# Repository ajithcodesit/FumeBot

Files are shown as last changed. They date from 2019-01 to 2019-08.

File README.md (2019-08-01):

# **FumeBot**

FumeBot is a Deep Neural Network controlled robot. The mobile robot is autonomous and can be fitted with a range of sensors for different purposes. 
This was completed as the final project for Master of Science in Mechatronics at Newcastle University situated in Newcastle upon Tyne, United Kingdom. This project is a published journal at MDPI as [*FumeBot: A Deep Convolutional Neural Network Controlled Robot*](#publication).

<p align="center">
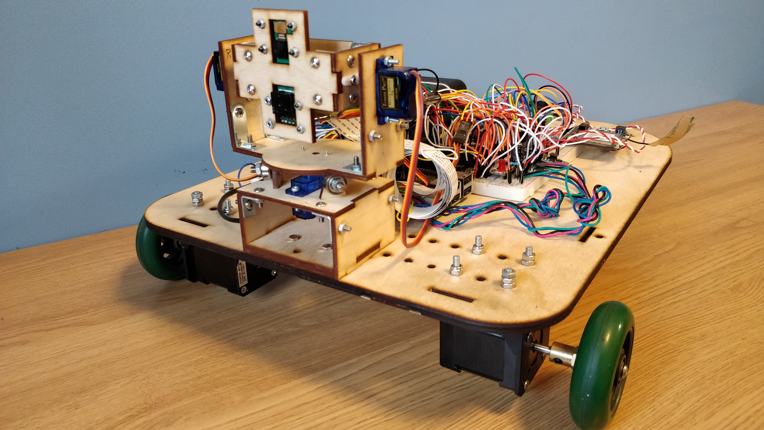
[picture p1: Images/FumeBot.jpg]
FumeBot

</p>

## Table of Contents
- [**FumeBot**](#fumebot)
  - [Table of Contents](#table-of-contents)
  - [Motivation](#motivation)
  - [Workings](#workings)
      - [The Mobile Robot](#the-mobile-robot)
      - [The Deep Neural Network](#the-deep-neural-network)
      - [The Graphical User Interface (GUI)](#the-graphical-user-interface-gui)
  - [Testing and Observations](#testing-and-observations)
  - [Requirements and Installation](#requirements-and-installation)
      - [Hardware Requirements](#hardware-requirements)
      - [Software Requirements](#software-requirements)
  - [Usage](#usage)
      - [Connecting to FumeBot](#connecting-to-fumebot)
      - [Controlling FumeBot](#controlling-fumebot)
      - [Collecting the Training Data](#collecting-the-training-data)
      - [The Deep Neural Network (AlexNet)](#the-deep-neural-network-alexnet)
      - [Data Communication and Video Transmission](#data-communication-and-video-transmission)
  - [Publication](#publication)
  - [Issues](#issues)

## Motivation

This was done as a masters final project. The idea was to check different kinds of deep neural network architectures that could be used for autonomous navigation. At the moment the only neural network that was tested is AlexNet which is a Deep Convolutional Neural Network by [Krizhvesky *et al*](https://papers.nips.cc/paper/4824-imagenet-classification-with-deep-convolutional-neural-networks.pdf).

## Workings

#### The Mobile Robot

FumeBot is a differential drive robot with a Raspberry Pi 3B and Arduino Mega 2560 on-board. The Raspberry is connected to a Raspberry Pi 5MP camera and also a Lepton 3 thermal camera. The Arduino interfaces with the stepper motor drivers, sensors and a 3G module, the data from which are sent back to the Raspberry through a UART connection. The Raspberry connects to a laptop through WiFi where the DNN is being run for inference. The DNN is being run on the laptop because if complex models are used then more processing power is available.

<p align="center">
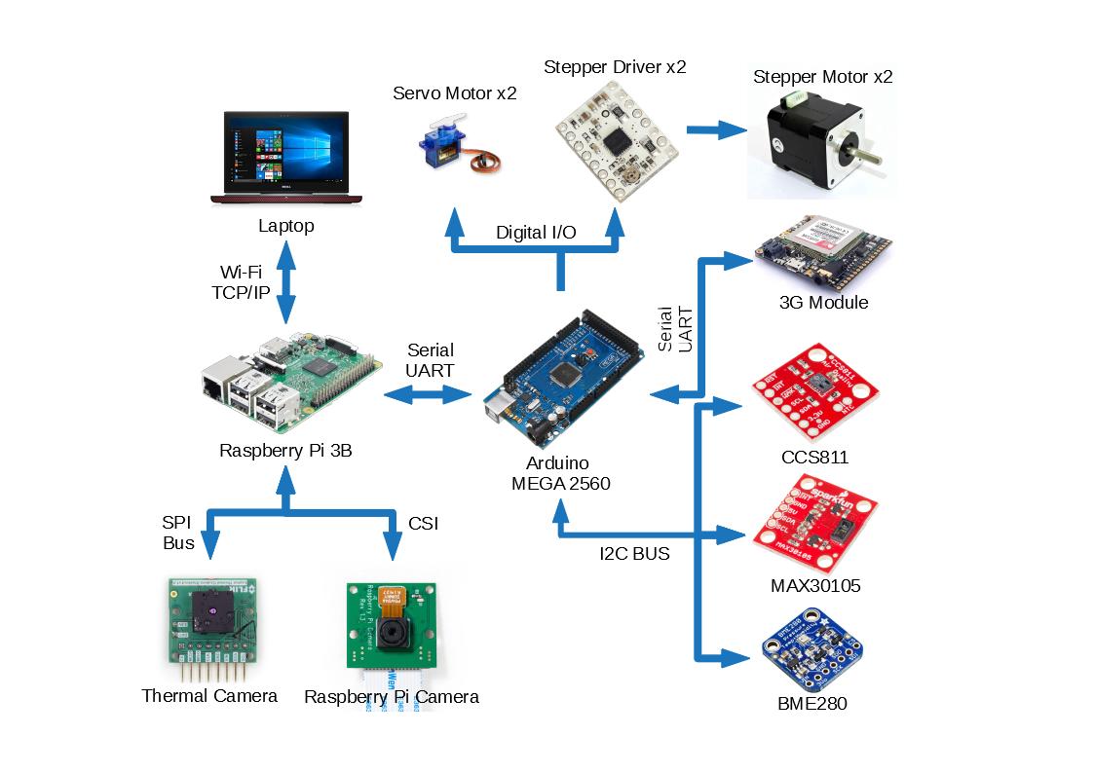
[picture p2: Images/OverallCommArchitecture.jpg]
Communication

</p>

The Raspberry Pi handles the heavy task of maintaining communication with the laptop, sending camera frames from both the RPi camera and Lepton back to the main computer. It also handles sending or receiving commands or data from the Main computer or Arduino microcontroller.

The robot is powered by two battery banks, one for driving the servo and stepper motors while the other is being used to power the Raspberry Pi 3, Arduino MCU, sensors and the 3G module. The range of motion available to the robot is shown below:

<p align="center">
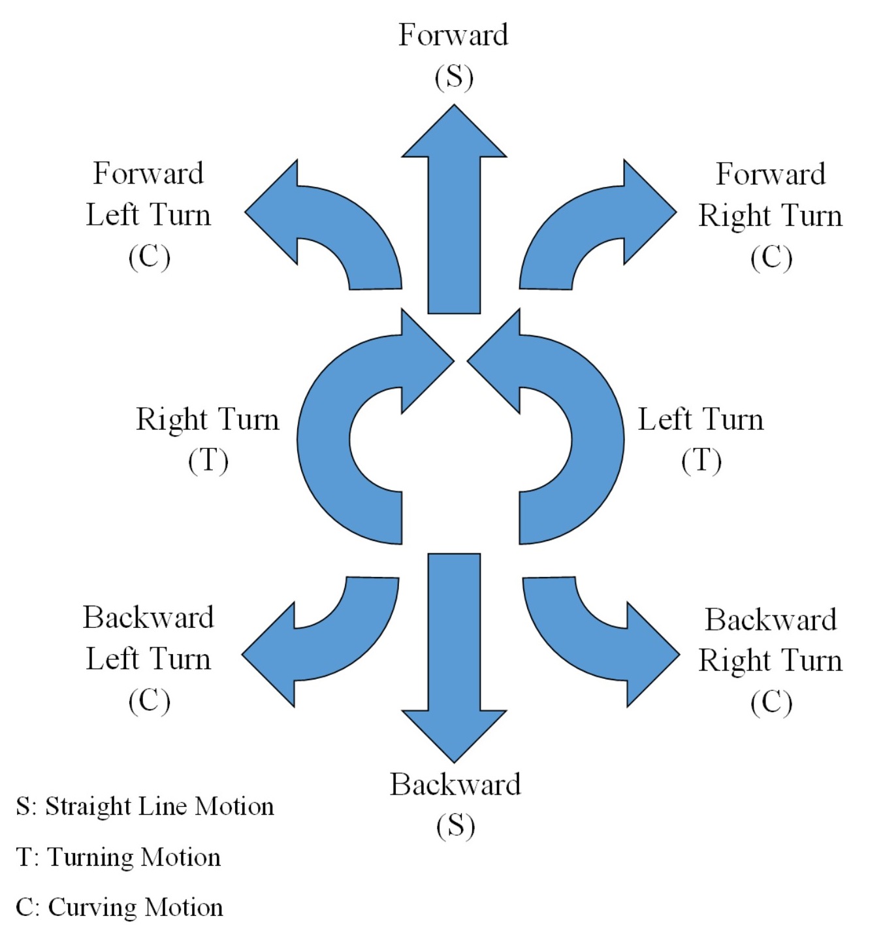
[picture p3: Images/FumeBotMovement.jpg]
Movement

</p>

In addition to controlling the robot's movement, the camera fork mount can be controlled as well to look around. The sensors carried by the robot are a gas sensor for measuring CO2 and TVOC (Total Volatile Organic Compound), particle sensor for detecting smoke and an environmental sensor for measuring pressure, temperature and humidity. Thresholds can be used to alert the user if the robot has detected smoke or high amounts of CO2 or TVOC. The alert can be sent over WiFi or through the 3G module by SMS if WiFi is not available.

#### The Deep Neural Network

As mentioned earlier the DNN used for the robot is a Convolutional Neural Network (CNN) which is a slight variation of AlexNet and can be seen in the image below.

<p align="center">
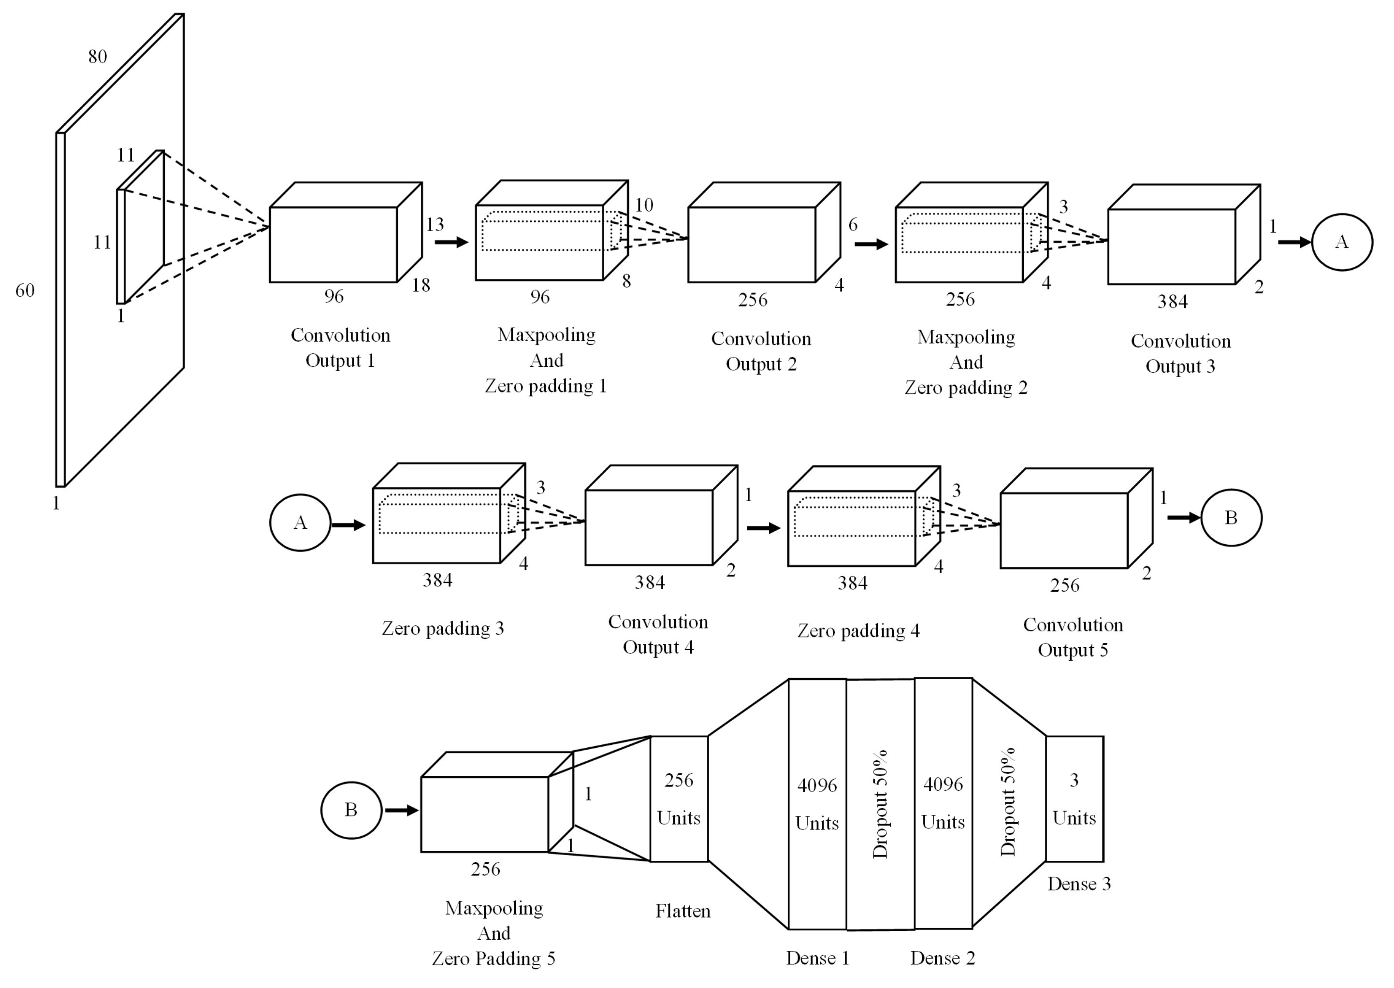
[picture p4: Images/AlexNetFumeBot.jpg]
CNN

</p>

For training the CNN, supervised learning was used in which data was collected by manually driving the robot and recording the camera frames along with the WASD key presses associated with that frame. The CNN was then trained to classify the correct key to press based on the frame received from the camera. The camera image given to the CNN was a grayscale 80x60 and the output from it is a one hot vector for example, `[0, 1, 0]` which is `[Forward left turn, Forward, Forward right turn]` of this `Forward` is selected as it is set to one.

The full range of motion available to the robot was not used to test whether the neural network could actually perform a simple task like navigating around an obstacle course. As a result only forward, forward left and forward right motion of the robot was used.

#### The Graphical User Interface (GUI)

A GUI was made to control the robot and to change the settings of the robot. The main function of the GUI is to display the image coming from the cameras, control the robot's movement and also the camera mount, record training data like the camera image and the key strokes as a one hot vector, video recording, changing the sensors thresholds and connection settings. The following is the GUI and the video stream coming from the robot displayed in the GUI respectively: 

<p align="center">
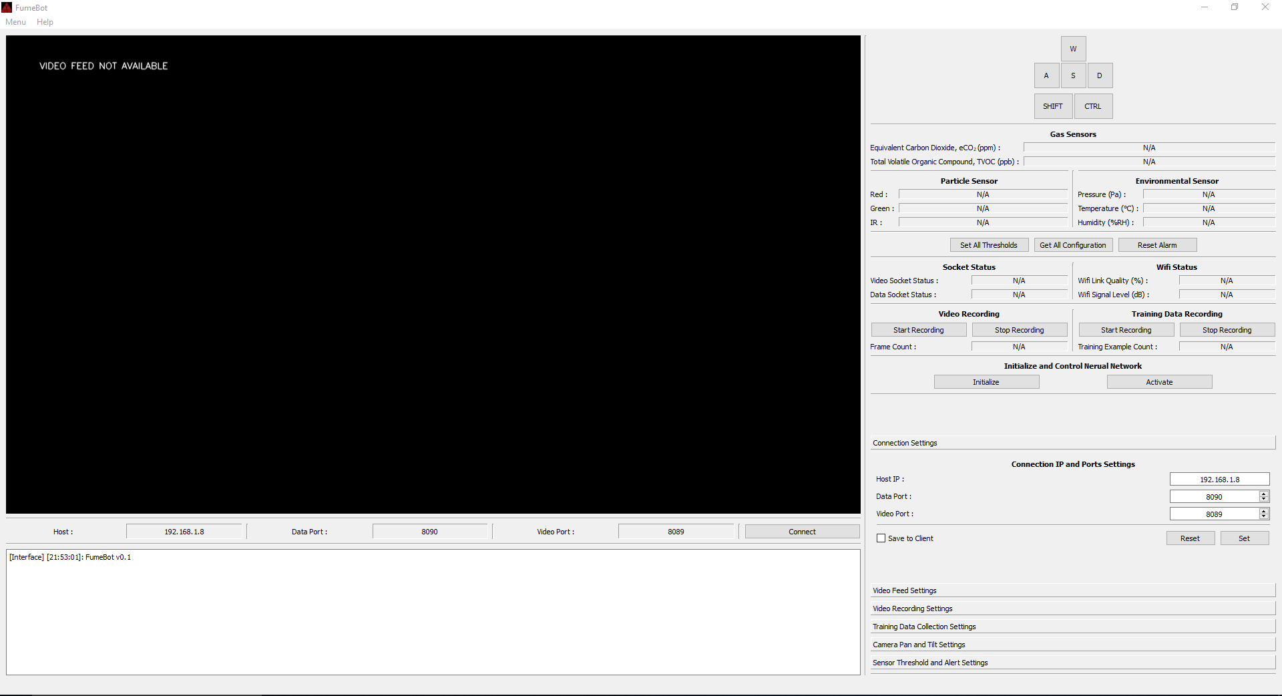
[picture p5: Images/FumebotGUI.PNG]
GUI

GUI video
<p align="center">

## Testing and Observations

The AlexNet CNN was trained on data collected from a simple obstacle course and was tested on the same and other obstacle courses to see if
it has generalized well. The obstacles when collecting the training data were orange cylinders but during testing other colors and different arrangement of
the obstacle was used to test whether it would confuse the neural network.

<p align="center">
FumeBot Lab Test Video
</p>

On testing the robot with different obstacle courses it was found that the robot has learned to navigate the courses. The obstacle color did not confuse the robot probably because grayscale images were used for training and inference which helped in not overfitting over the color of the obstacle used. But human biases
were learned by the network, for example, in order to make it obvious to the network to avoid the obstacle, it was intentionally driven up to the obstacle and avoided at the last moment which caused the neural network to follow the obstacle if moved and then avoid it. The robot was able to stay in the obstacle 
course and complete it but did make mistakes and collided with the obstacle. This is caused by not using a wide angle lens and using the standard RPi camera lens which has a limited field of view.

## Requirements and Installation

This section describes the the hardware and software requirements for FumeBot. The robot is designed in Autodesk Inventor 2018. The parts and assembly files are available [here](./FumeBot-Design/).

#### Hardware Requirements
The schematics for wiring up FumeBot can be found [here](./FumeBot-Circuit_Design/Fumebot%20Circuit.pdf).
- Raspberry Pi 3B
- Raspberry Pi Camera v1.3 (5MP)
- [FLIR Lepton 3 Camera](https://groupgets.com/manufacturers/flir/products/lepton-3-0) 
- [Adafruit FONA 3G Cellular + GPS Breakout (SIMCom SIM5320A)](https://learn.adafruit.com/adafruit-fona-3g-cellular-gps-breakout/downloads)
- Arduino MEGA 2560
- [Adafruit BME280 (Environmental Sensor)](https://www.adafruit.com/product/2652)
- [SparkFun CCS811 (Gas Sensor)](https://www.sparkfun.com/products/14193)
- [SparkFun MAX30105 (Particle Sensor)](https://www.sparkfun.com/products/14045)
- [DRV8834 Stepper Motor Driver](https://www.pololu.com/product/2134)
- [Pololu Boost Regulator](https://www.pololu.com/product/799)
- [Stepper Motors](https://www.omc-stepperonline.com/nema-17-bipolar-18deg-44ncm-623ozin-085a-53v-42x42x48mm-4-wires-17hs19-0854s.html)
- [TowerPro SG90 Servo Motors](http://www.ee.ic.ac.uk/pcheung/teaching/DE1_EE/stores/sg90_datasheet.pdf)
- BC547 Transistors
- RGB LED (Used as a status LED)

#### Software Requirements
The following software needs to be installed before running the main programs.

- For Windows PC (The GUI application was not tested on Linux)
  - OpenCV 3.4.3
  - Numpy 1.14.5
  - TensorFlow 1.10.0
  - Keras 2.2.2
  - Pandas 0.23.4 
  - PyQt4 4.11.3
  
  The above packages are for Python 3.6. Both OpenCV and PyQt4 can be installed using pip from [here](https://www.lfd.uci.edu/~gohlke/pythonlibs/). The rest can be installed by just using pip.

- For Raspberry Pi 3B (The RPi 3B application needs to be run with python 2.7)
  - PySerial 3.4
  - OpenCV 3.4.1
  - Numpy 1.14.2
  - RPI.GPIO
  
  The above packages are for Python 2.7. OpenCV needs to compiled from source and installed using instructions 
  found [here](https://www.pyimagesearch.com/2015/07/27/installing-opencv-3-0-for-both-python-2-7-and-python-3-on-your-raspberry-pi-2/). OpenCV was installed without Python Virtual Environment.

  The `FumeBot-RPi3B` file needs to be copied to `/home/pi/` directory of the Raspberry Pi and the `botsetup.sh` script should be run. This will create a service that starts every time the Raspberry boots and can be controlled using `systemctl`.

  ```bash
  # To run the script
  sudo chmod +x botsetup.sh
  ./botsetup.sh

  # To enable or disable the FumeBot service
  sudo systemctl enable fumebot.service
  sudo systemctl disable fumebot.service

  # To start or stop the FumeBot service
  sudo systemctl start fumebot.service
  sudo systemctl stop fumebot.service
  ```

- For Arduino MEGA 2560 
  - Adafruit BME280 Library
  - Adafruit FONA Library
  - SparkFun CCS811 Library
  - SparkFun MAX3010x Pulse and Proximity Sensor Library
  
  The `FumeBOT.ino` file must be flashed to the Arduino MEGA and can be found [here](./FumeBot-Firmware/FumeBOT/).

## Usage

This section describes how to use the software and to control the robot. Additional information about source code is also provided.

#### Connecting to FumeBot

The FumeBot GUI application needs to be started first by running `python FumeBot.py` on the laptop or main computer, then the connection setting needs to be changed to IP of the host computer (Laptop) to open the ports and start listening. In Window, the IP address of the machine can be found out by running `ipconfig` in command prompt and looking at the IPv4 Address section. The GUI running on the PC is the server and the Raspberry is the client, both the machines needs to have the same IP and ports for them to be able to connect. The IP and ports configuration of Fumebot can be changed in the `FumeBot-Rpi3B/bot_config.ini` file. The FumeBot service needs to be running as well.

#### Controlling FumeBot

The WASD keys can be used to control the movement of the robot and the mouse can be used to control the camera mount to tilt and pan. The mouse needs to be dragged across the video display area while holding down the left mouse button. The video capture settings can be changed to an appropriate resolution so that video lag can be reduced.

#### Collecting the Training Data

The training data recording can be started or stopped by pressing 'T' key or the "Start Recording" button can be used in the training data section. The training data is collected in the format of an image and the corresponding key pressed on receiving that image. The training data is saved as `.npy` file with an associated `.meta` file that stores the disabled keys and the order of enabled ones. For an example of reading the `.npy` file, `ViewTrainingData.py` could be run. Preprocessing maybe needed to get the data ready for training the DNN and an example of this can found in `DataSetPreprocessing.py`.

#### The Deep Neural Network (AlexNet)

The AlexNet CNN model is defined in `DeepNeuralNetworkModel.py` the methods of which are loaded into `FumeBotGUI/FumeBotDNN.py`. The model is loaded and weights are applied in the constructor of the `FumeBotDNN` class. The `dnn_prediction_function` is used for inference and the output of this function is the required key the CNN wants to send to the robot. The key classification should be a one-hot vector, for example, `[1, 0, 1]`. The predicted key press vector is emitted as a signal in PyQt to the main GUI application and is handled by the `handle_dnn_key_press` function.

For inference on images coming from the robot, the DNN must be first initialized by pressing the 'I' key or "Initialize" button. To start the prediction the 'N' key can be used to toggle it or "Activate" button can be pressed. The `FumeBotDNN.py` is loaded into the main GUI application `FumeBot.py` in which the `dnn_prediction_function` mentioned earlier is run inside the `update_video_feed_display` function.

#### Data Communication and Video Transmission

The data communication and reception of video stream is done in `FumeBotGUI/FumeBotSockComm.py`. The handling of data is done in the `handle_socket_data` function and the image frames from the camera is handled in the `get_socket_stream_frames` function in the main GUI. The data is exchanged between the `FumeBotSockComm.py` and `FumeBot.py` in the form of PyQt signals as mentioned above in the case of the DNN.

The frames coming from the camera are in JPEG format and is then rendered in the GUI video frame. The figure shown below shows how the video is sent from the client (Robot) to the Server (Fumebot GUI application). Both the RPi camera and the Lepton thermal camera follows the same procedure for transmission of video.

<p align="center">
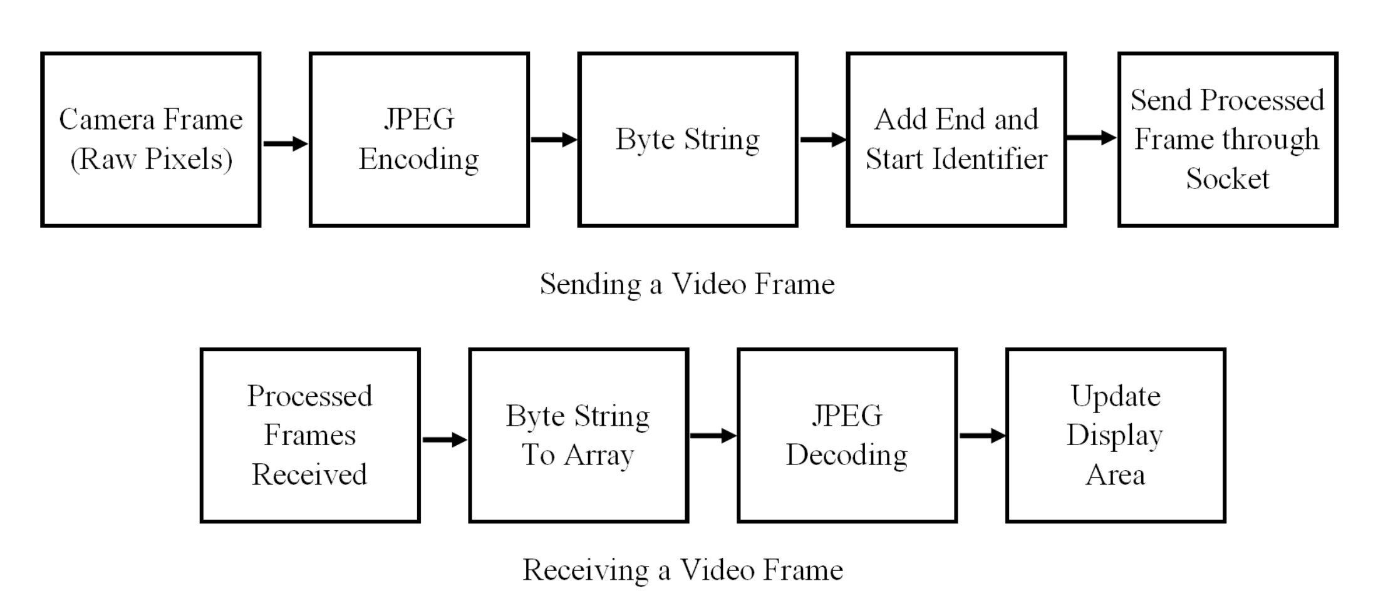
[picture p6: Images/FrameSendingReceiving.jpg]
Video TX RX

</p>

If other data needs to be sent from the robot, the `handle_socket_data` function needs to be modified. All the data communication from the Raspberry and Window PC needs to be in the following format:
```
$<CMD>,<DATA1>,<DATA2>,…,<DATA(n-1)>,#
```
Data communication between the Raspberry and Arduino is in the following format:

```
<CMD>,<DATA1>,<DATA2>,…,<DATA(n-1)>,\n
```
All the data are sent and received in plain string format.

## Publication

[Thomas, A.; Hedley, J. FumeBot: A Deep Convolutional Neural Network Controlled Robot. *Robotics* **2019**, 8, 62.](https://doi.org/10.3390/robotics8030062)

## Issues

The following are some of the know issues observed during testing.

- The `FumeBotMain.py` which is ran on the client side can sometimes crash with an error caused by OpenCV.
- Python 2.7 is used in the client side because OpenCV could not be installed for Python 3.6. Later this was resolved but not tested. 
- The FLIR Lepton 3 thermal camera module freezes after a few minutes of usage. 
- Data built up in the client side causes a lag in getting the real time sensor measurements displayed on the GUI.
- The initialization of the DNN is slow.
- Saving the training data takes a long time if the data held in the list is large.

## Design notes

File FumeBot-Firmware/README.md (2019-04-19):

## **Additional Information about the Firmware**

#### Firmware Usage
The `FumeBOT` folder needs to be opened in Arduino 1.8.7 or higher and the `FumeBOT.ino` file needs to be flashed to
an Arduino MEGA 2560 only. This is because the timers of the microcontroller are now used for generating the square wave required to drive the stepper motor and registers specific to the Atmel ATmega2560 microcontroller are changed.

#### Modification to Servo Libraries
The above modification to the timer register meant some changes needed to be applied to the `Servo.cpp`, `Servo.h` and `ServoTimers.h` files. The changes to these files are necessary because all the timers in the microcontroller are initially setup to generate PWM outputs and the above register modification to generate a required frequency square wave interferers with servo library timer setup. The library is also required to control the pan and tilt servos for the camera fork mount.

To fix the above-mentioned problems, a copy of the servo library was made and altered to not make use of the timers required to generate the square wave for the stepper drivers. The libraries were then renamed to `ServoMod.cpp`, `ServoMod.h` and `ServoTimersMod.h` so that it does not interfere with the original servo libraries provided by Arduino. This was done instead of modifying the original servo libraries because the changes were only needed for this application.

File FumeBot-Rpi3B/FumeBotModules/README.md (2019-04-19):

## **Modules for Mobile Robot Side**

#### Communication modules for the Robot
The communication between the robot and GUI application is achieved by using the `FumeBotSocketComm.py` which uses TCP sockets for streaming data. On the other hand the communication between the Raspberry Pi and the Arduino microcontroller is realized through `FumeBotSerialComm.py` module. The serial communication is through a standard UART port available on both the Arduino MEGA and Raspberry Pi. 

The default UART available on Raspberry Pi 3B GPIO is the Mini UART which is inferior compared to the UART used for the Bluetooth modem. Therefore, the UARTs are switched so that the better one is available at the GPIO. More information on how to do this is available by following this [link](https://www.raspberrypi.org/documentation/configuration/uart.md).

#### The FLIR Lepton 3 Module
To communicate with the Lepton 3 thermal camera the `Lepton3capture.c` was slightly modified from the original available [here](https://github.com/lukevanhorn/Lepton3/blob/master/capture/capture.c). Since the main program for the robot is written in python the `Lepton3capture.c` file is compiled into shared object file and is then loaded into `Lepton3CapLib.py` python module which breaks out the necessary functions available in the original C file. The `Lepton3CapLib.py` file is then imported by `FumeBotSocketComm.py` to get the frames from the thermal camera in a thread and send it to the GUI application.

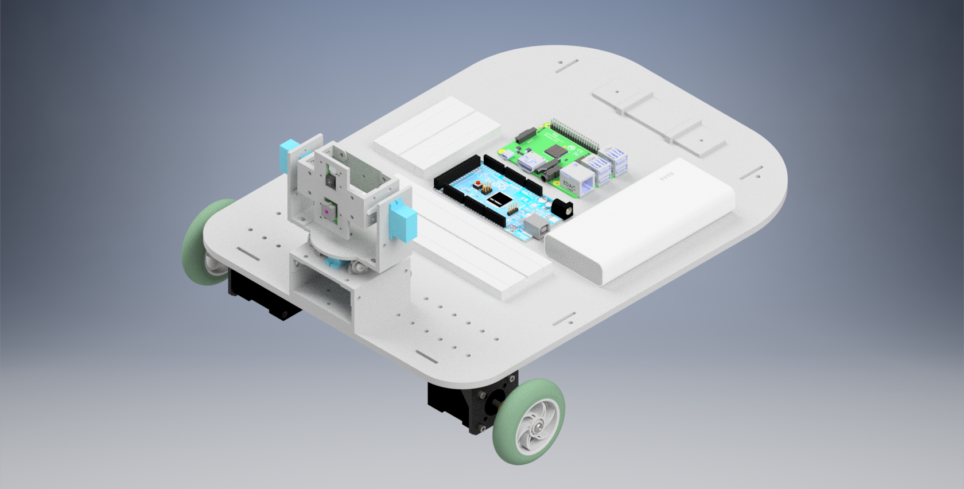
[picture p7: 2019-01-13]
FumeBot-Design/Renders/FumeBOT Fork Mount - isometric view.png

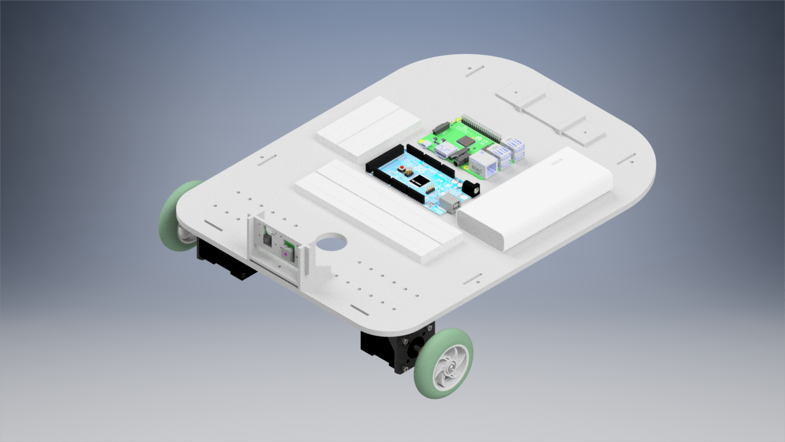
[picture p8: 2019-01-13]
FumeBot-Design/Renders/FumeBOT- isometric view.png

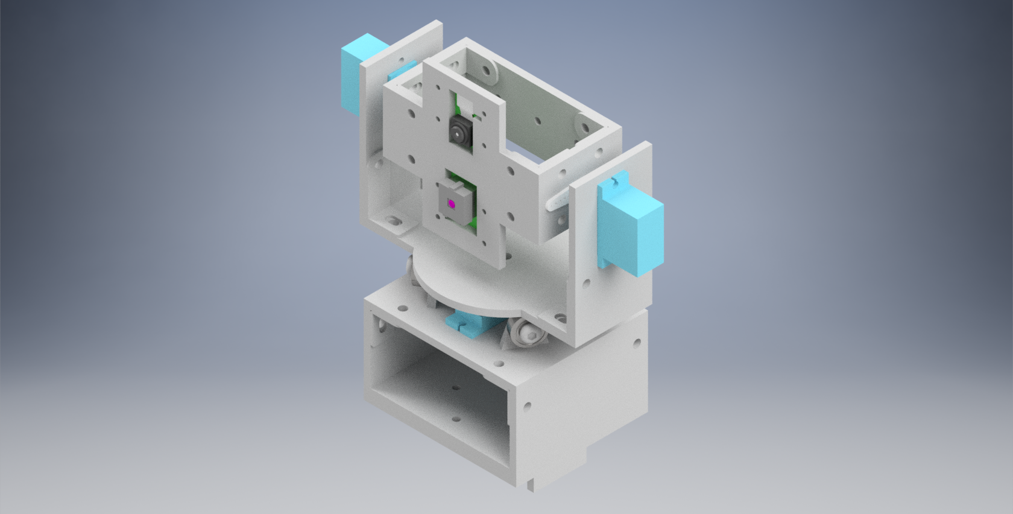
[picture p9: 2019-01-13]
FumeBot-Design/Renders/Fork Mount - isometric view.png

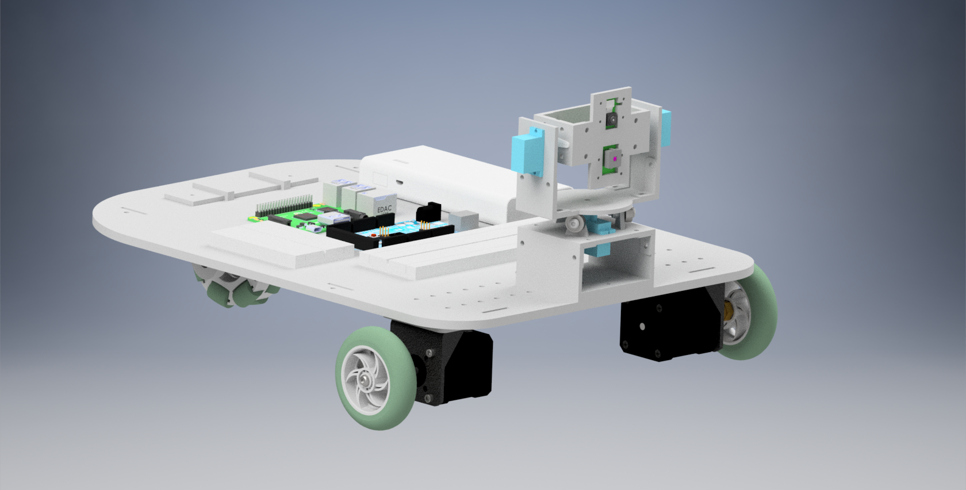
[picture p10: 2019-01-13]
FumeBot-Design/Renders/FumeBOT Fork Mount - low angle view.png

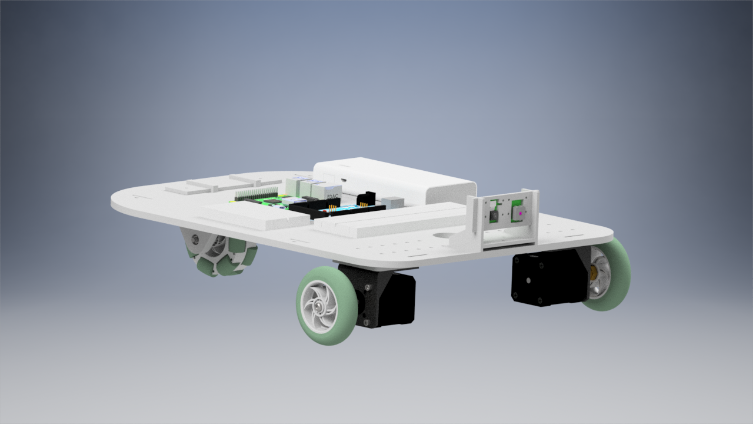
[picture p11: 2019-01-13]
FumeBot-Design/Renders/FumeBOT - Low angle view.png

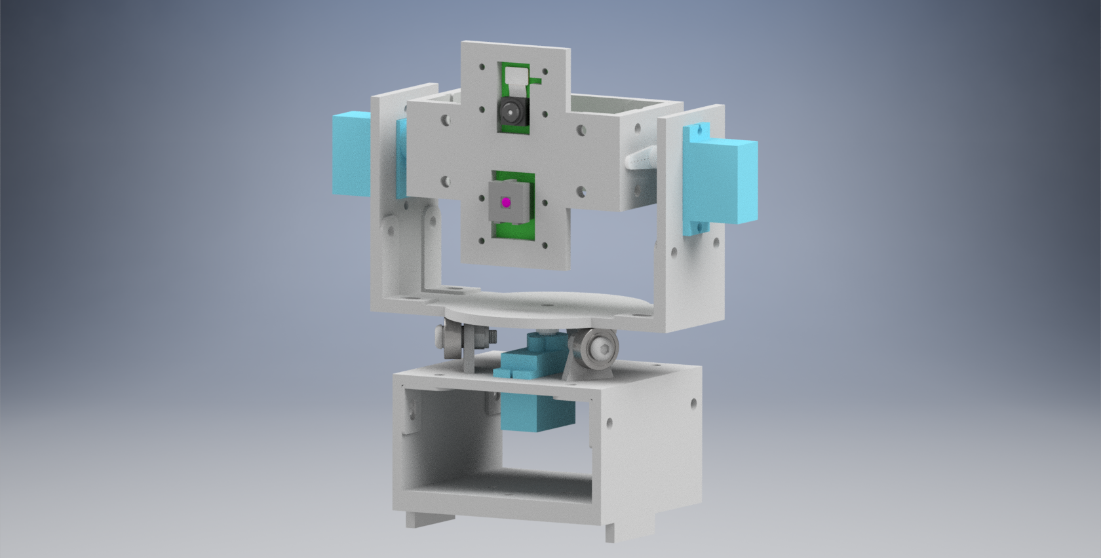
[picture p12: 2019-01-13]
FumeBot-Design/Renders/Fork Mount - Low angle view.png

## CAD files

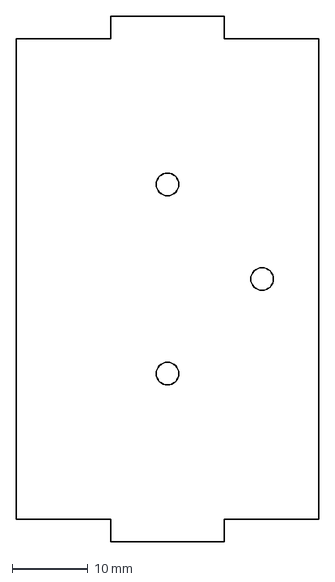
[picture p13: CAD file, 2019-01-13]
FumeBot-Design/DXF files/Mobile Bot Chassis DXF files/Camera cross bar-3mm-x1.dxf
40.0 x 69.5 mm

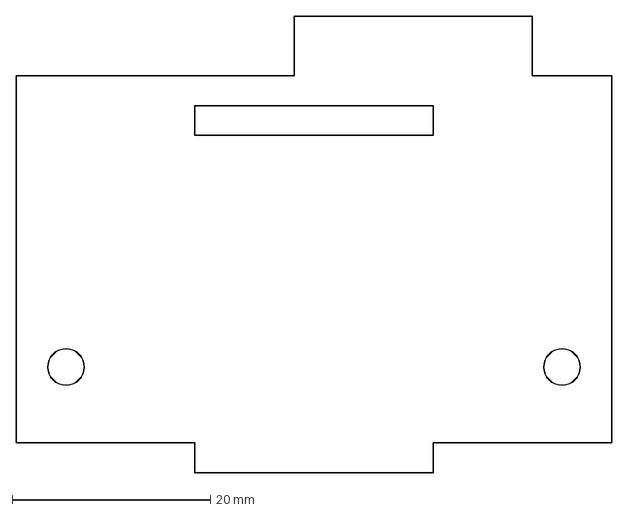
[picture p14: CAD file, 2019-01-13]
FumeBot-Design/DXF files/Pan and Tilt DXF files/Pan base top side bars-3mm-x2.dxf
60.0 x 46.0 mm

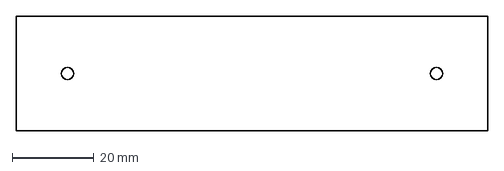
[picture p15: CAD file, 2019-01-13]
FumeBot-Design/DXF files/Mobile Bot Chassis DXF files/Mecanum support lock bar-3mm-x1.dxf
115.0 x 28.0 mm

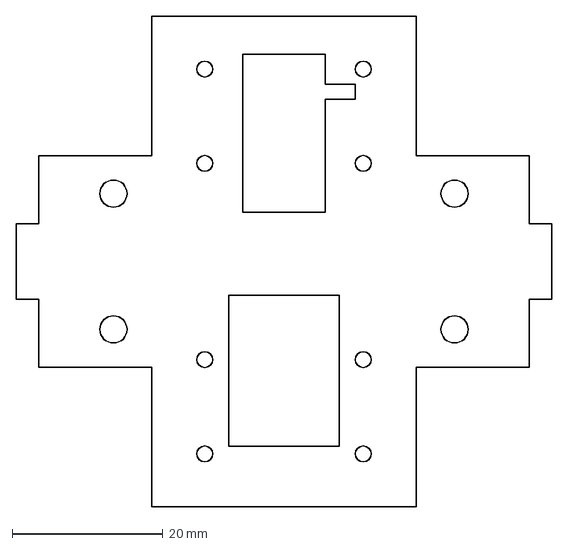
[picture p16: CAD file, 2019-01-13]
FumeBot-Design/DXF files/Pan and Tilt DXF files/Camera holder plate-3mm-x1.dxf
71.0 x 65.0 mm

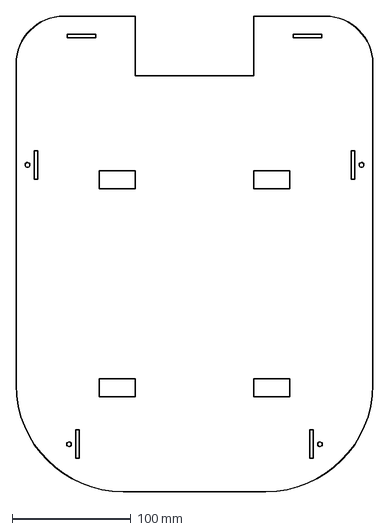
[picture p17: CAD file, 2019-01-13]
FumeBot-Design/DXF files/Mobile Bot Chassis DXF files/Top plate-3mm-x1.dxf
300.0 x 400.0 mm

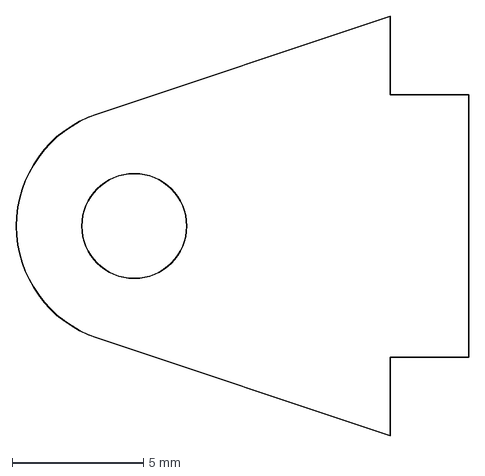
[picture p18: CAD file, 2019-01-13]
FumeBot-Design/DXF files/Pan and Tilt DXF files/Bearing risers-3mm-x3.dxf
17.2 x 16.0 mm

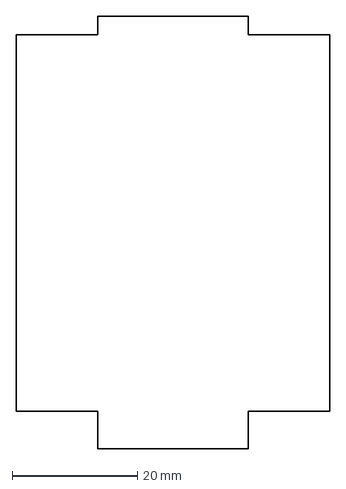
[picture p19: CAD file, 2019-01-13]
FumeBot-Design/DXF files/Mobile Bot Chassis DXF files/Base and top seperator-3mm-x6.dxf
50.0 x 69.0 mm

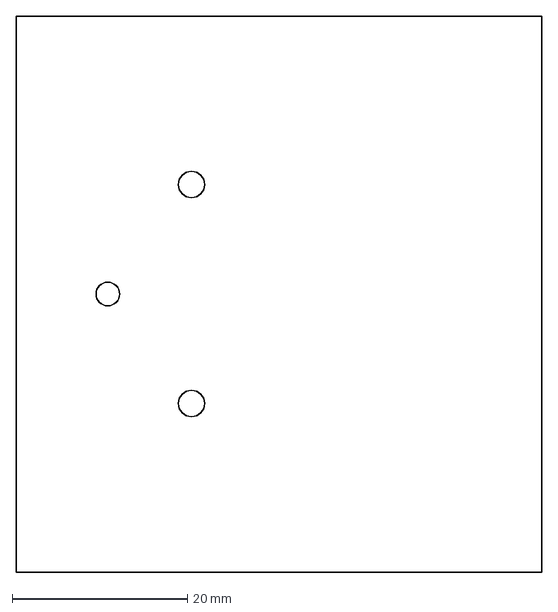
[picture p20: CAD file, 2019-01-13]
FumeBot-Design/DXF files/Pan and Tilt DXF files/Pan cross bar spacer-3mm-x1.dxf
60.0 x 63.5 mm

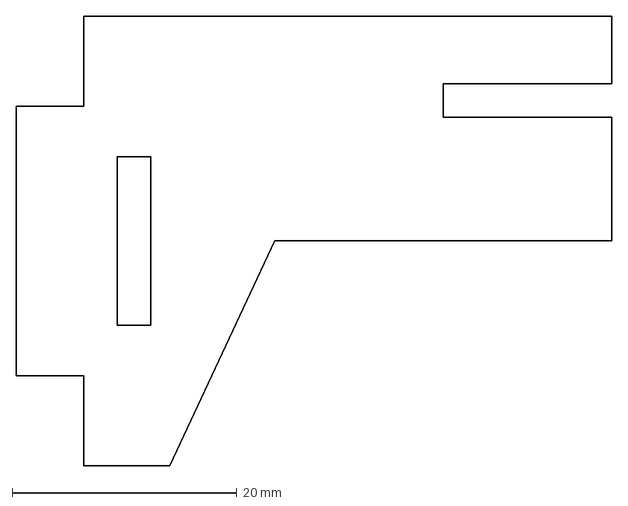
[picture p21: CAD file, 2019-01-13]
FumeBot-Design/DXF files/Mobile Bot Chassis DXF files/Camera bracket raiser-3mm-x2.dxf
53.0 x 40.0 mm

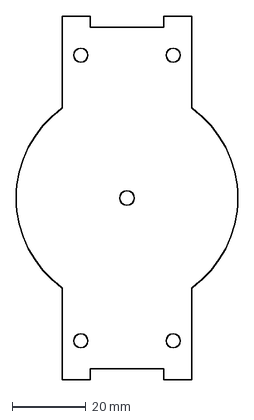
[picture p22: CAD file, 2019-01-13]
FumeBot-Design/DXF files/Pan and Tilt DXF files/Camera raiser-3mm-x1.dxf
60.0 x 98.4 mm

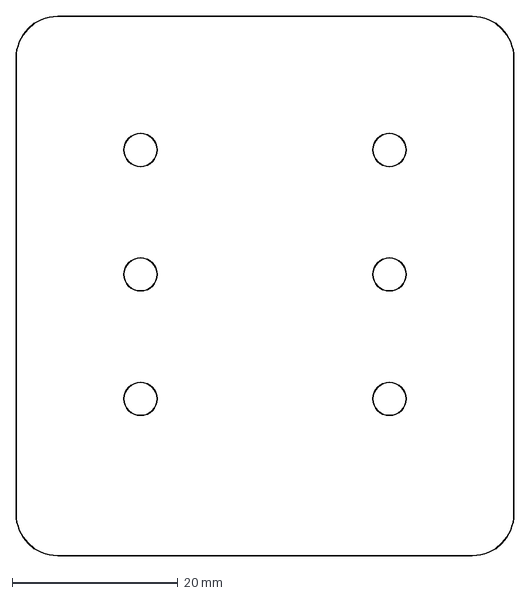
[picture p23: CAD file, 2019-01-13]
FumeBot-Design/DXF files/Mobile Bot Chassis DXF files/Wheel height spacer-6mm-x2.dxf
60.0 x 65.0 mm

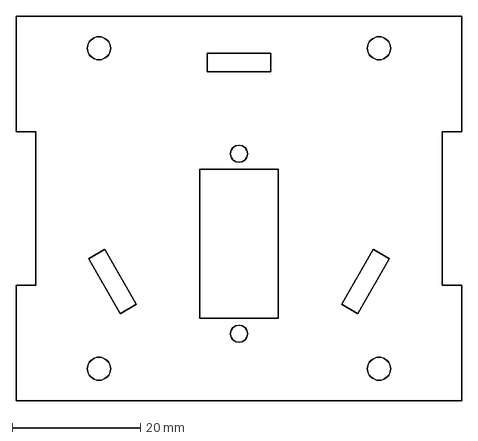
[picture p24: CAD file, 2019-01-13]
FumeBot-Design/DXF files/Pan and Tilt DXF files/Camera pan base-3mm-x1.dxf
69.5 x 60.0 mm

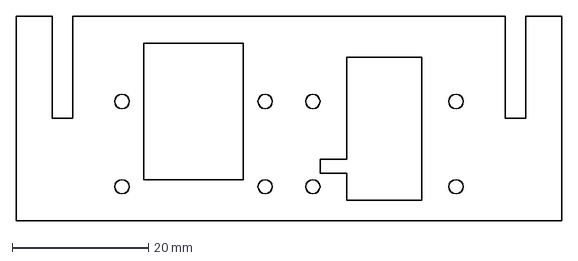
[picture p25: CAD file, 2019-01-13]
FumeBot-Design/DXF files/Mobile Bot Chassis DXF files/Camera bracket-3mm-x1.dxf
80.0 x 30.0 mm

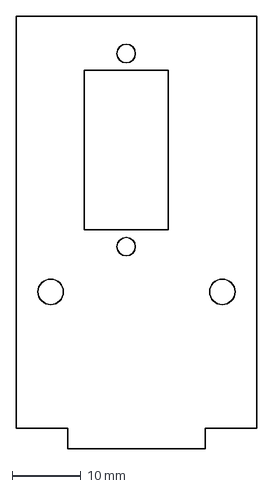
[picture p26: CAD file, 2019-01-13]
FumeBot-Design/DXF files/Pan and Tilt DXF files/Camera mount raiser-3mm-x2.dxf
35.0 x 63.0 mm

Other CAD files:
FumeBot-Design/DXF files/Mobile Bot Chassis DXF files/Mecanum wheel support-6mm-x2.dxf
FumeBot-Design/DXF files/Pan and Tilt DXF files/Tilt back support with counter balance option-3mm-x1.dxf
FumeBot-Design/DXF files/Mobile Bot Chassis DXF files/Base-6mm-x1.dxf
FumeBot-Design/DXF files/Pan and Tilt DXF files/Camera mount side bars-3mm-x2.dxf
FumeBot-Design/Angle brackets/Angle bracket long.ipt
FumeBot-Design/Angle brackets/Angle bracket short.ipt
FumeBot-Design/Base and top seperator.ipt
FumeBot-Design/Base.ipt
FumeBot-Design/Battery.ipt
FumeBot-Design/Bearing lockers.ipt
FumeBot-Design/Bearing.ipt
FumeBot-Design/Camera bracket raiser.ipt
FumeBot-Design/Camera bracket.ipt
FumeBot-Design/Camera cross bar.ipt
FumeBot-Design/Camera mount assembly.iam
FumeBot-Design/DXF files/Mobile Bot Chassis DXF files/Bearing lockers-3mm-x2.dxf
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

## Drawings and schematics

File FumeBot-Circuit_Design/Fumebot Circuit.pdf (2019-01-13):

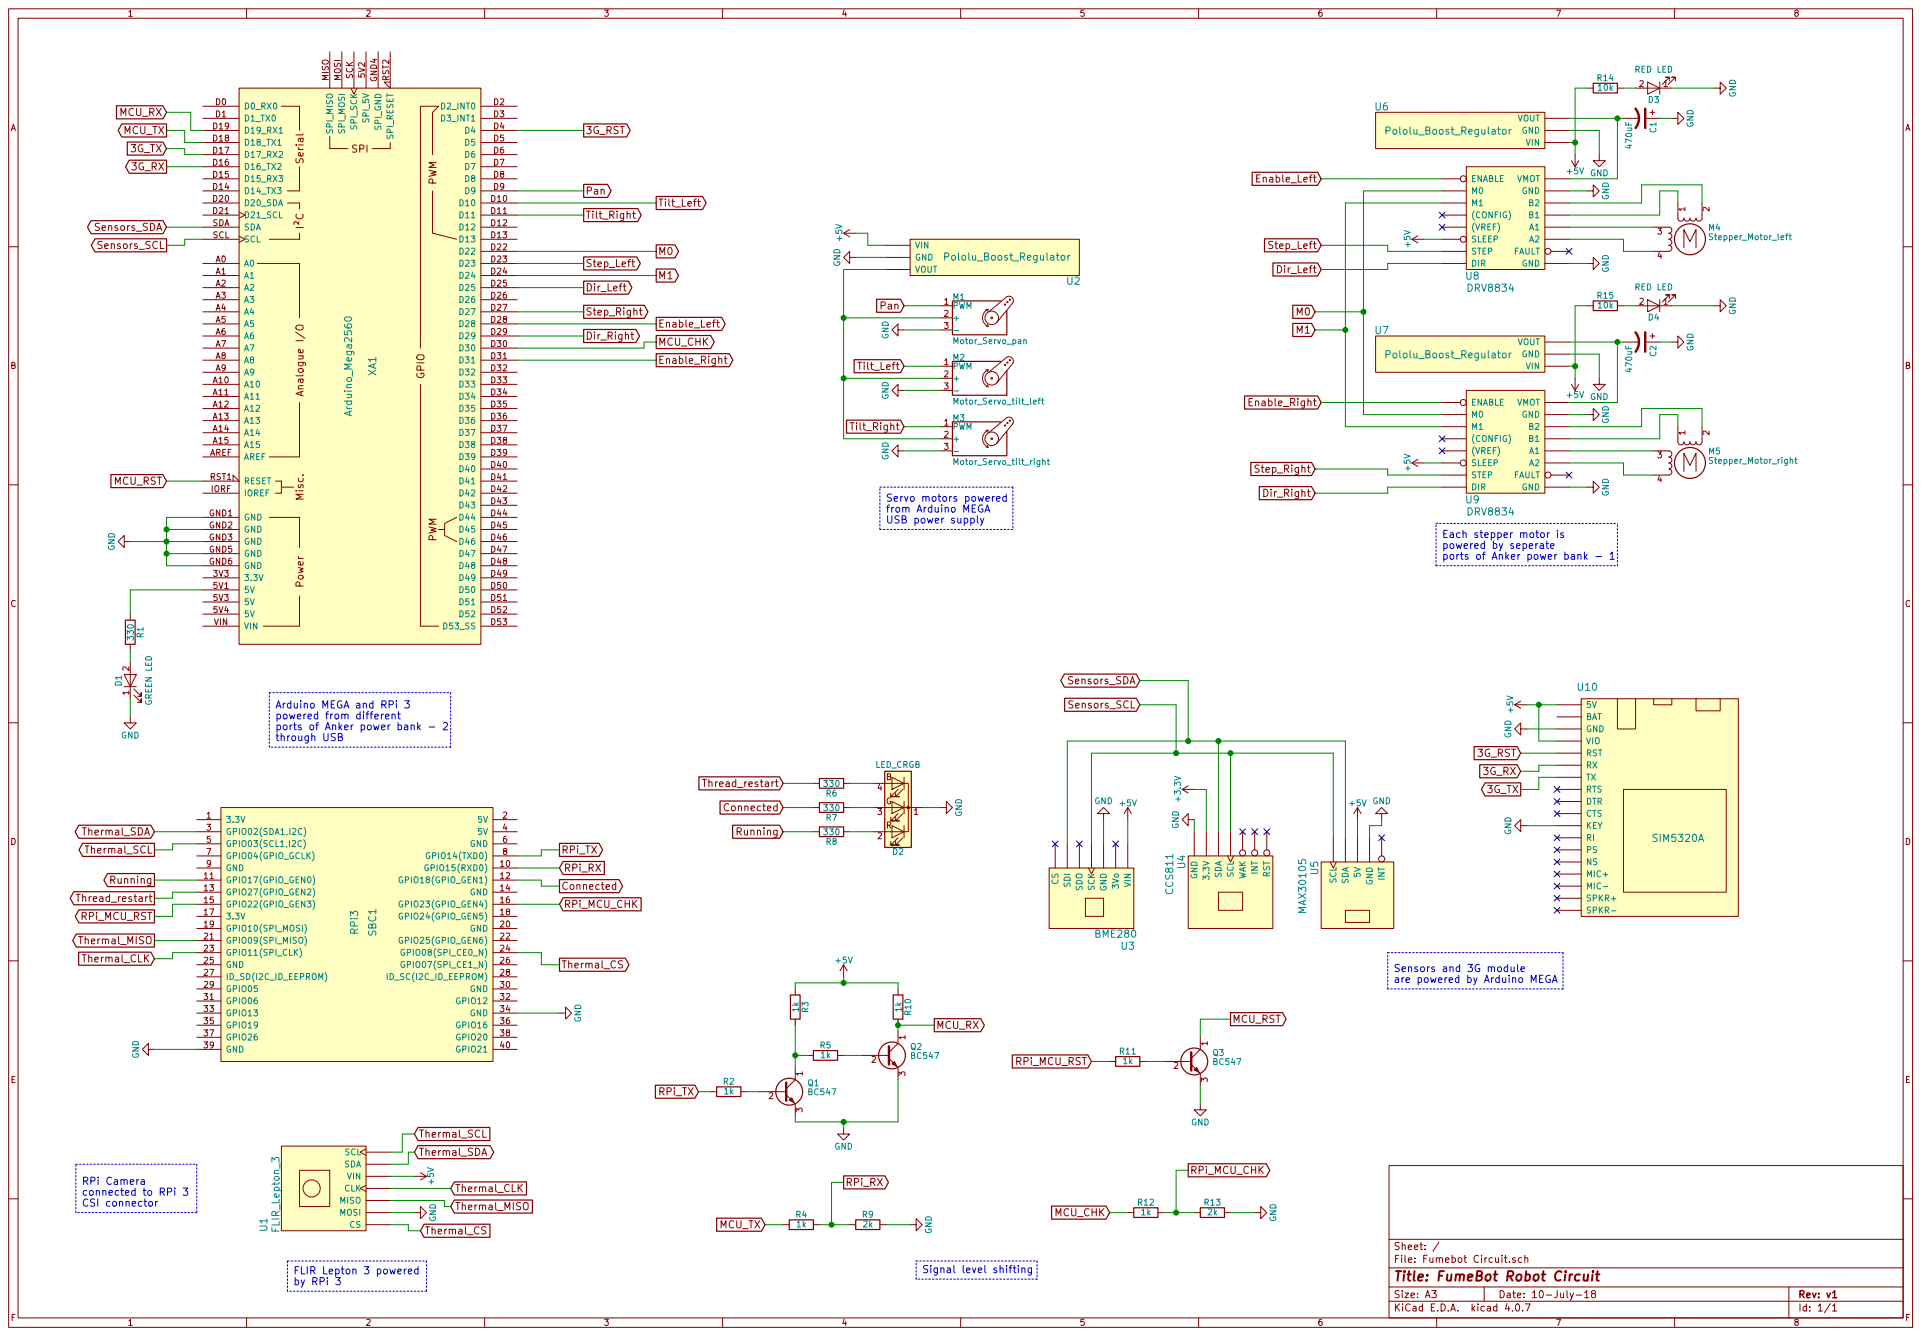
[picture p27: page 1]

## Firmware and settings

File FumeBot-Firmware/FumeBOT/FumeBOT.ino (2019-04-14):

#include <Wire.h>
#include "MAX30105.h"
#include <SparkFunCCS811.h> //Use version 1.0.0 of the library
#include <Adafruit_BME280.h>
#include "Adafruit_FONA.h"
#include "ServoMod.h"

//#############################################################SENSORS AND PERIPHERALS############################################################

const uint8_t CCS811_ADDRESS=0x5B;  //IIC address for CCS811
const uint8_t FONA_RST=4;

const uint8_t MCU_RDY_PIN=30;  // This pin is used to tell the RPi that it is ready

HardwareSerial *fonaSerial = &Serial2;

MAX30105 particle_sensor;
CCS811 air_quality(CCS811_ADDRESS);
Adafruit_BME280 bme; //For IIC mode
Adafruit_FONA fona=Adafruit_FONA(FONA_RST);

// Sensor variables
const unsigned int SENSOR_READING_DELAY=150;  //In ms

struct sensor_thresholds  //Struct to store the thresholds for the different sensor
{
  //For gas sensor
  unsigned int eCO2=1000;
  unsigned int TVOC=100;

  //For particle sensor
  unsigned int red=10000;
  unsigned int green=10000;
  unsigned int ir=10000;

  boolean updated=false; //Variable to say whether the thresholds were updated to the required values or not
}thresh;

//3G module variables
struct sms_comm
{
  boolean sms_repeat_disable=false; //This can be used to rearm the sms alert
  boolean sms_send=false;  //Boolean to say whether the SMS was sent or not
  boolean enable_sms=false; //Boolean to say whether the SMS is allowed or not
  char sms_num[21]="0000000000";  // Number to send the alert to
  char alert_msg[140]="Test message";
  uint8_t sms_tries=0;
  const uint8_t max_tries=3;
}alrt_com;

enum ack_cfg_codes //These codes are sent pack to say that these parameters have been updated by the raspberry pi
{
  GAS_THR=1,
  PAR_THR=2,
  SMS_SET=3,
  RST_ALM=6,
};

//#############################################################STEPPER DRIVER############################################################
//Microstepping pins
const uint8_t ms1=22;
const uint8_t ms2=24;

//Eanble pin
const uint8_t enb_l=28;
const uint8_t enb_r=31;

//Step and direction for the left motor
const uint8_t stp_l=23;
const uint8_t dir_l=25;

//Step and direction for the right motor
const uint8_t stp_r=27;
const uint8_t dir_r=29;

enum prescalers  //Prescalers for Timer 3 and 4
{
  PS0=0,   //No clock source
  PS1=1,   //No prescaling
  PS8=8,   //Clock I/O divider of 8
  PS64=64,  //Clock I/O divider of 64
  PS256=256, //Clock I/O divider of 256
  PS1024=1024 //Clock I/O divider of 1024
};

const uint32_t F_CLK_IO=16e6;  //CPU clock frequency 16*10^6

//This is the absolute maximum limit of the RPM that is allowed
const float ABS_MAX_RPM=1000.0;
const float ABS_MIN_RPM=0.0357;

//Robot motion limits
const float MAX_MOV_SPEED=0.30; //Maximum movement speed m/s
const float MIN_MOV_SPEED=0.20; //Minimum movement speed m/s

const float MAX_TURN_SPEED=75.0; //Degrees/s
const float MIN_TURN_SPEED=45.0; //Degrees/s

const float TURN_RADIUS=0.332; //In meters

//Differential geometry
const float WHEEL_RADIUS=0.035; //In meters
const float HALF_AXLE=0.166; //In meters

//This the actual RPM used
const float MAX_RPM=200; //Can go up to 200 RPM
const float MIN_RPM=0.5; //Can go down to 0.5 RPM
const int MAX_STEPS=50; //Maximum allowed no of steps
volatile int BUF_STEPS=MAX_STEPS/2; //Steps after which the steps completed boolean will be set true [This is done to act as buffer]
const float DPS=1.8; //Degree Per Step of the stepper motor
const uint8_t MS=1; //Microstepping (1 to 16)

//Rotation direction constants
const boolean LEFT_CLK=HIGH;
const boolean LEFT_ACLK=LOW;

const boolean RIGHT_CLK=HIGH;
const boolean RIGHT_ACLK=LOW;

//Enable or disable stepper motors drivers
const boolean DISABLE_SMOT=HIGH;
const boolean ENABLE_SMOT=LOW;

struct stepping //Contains the variable used by the right and left motor
{
  uint8_t step_pin;
  uint8_t dir_pin;
  volatile int step_count=0; //The steps that were done
  volatile int req_steps=0; //This is compared to the step count variable
  volatile uint16_t req_count=0; //This used to change the speed in the ISR [set_rpm should not be called outside the setup]
  volatile boolean steps_completed=true; //Variable to say whether the steps were completed or not
  volatile boolean direct; //Sets the direction the motor has to turn
  volatile boolean start_rotation=true; //To start rotation
  volatile boolean until_left_stops=false; //For rotating right stepper until left stops
  volatile boolean until_right_stops=false; //For rotating left stepper until right stops
}left,right;

struct driver_config //Microstepping variables
{
  uint8_t ms1,ms2; //Stores the microstepping pins (Both motor uses the same pins)
  uint8_t enb_left; //Stores the enable pin for left
  uint8_t enb_right; //Stores the enable pin for right
  boolean auto_enb_disb=true; //Whether the motor will be disabled automatically when not in used
  boolean override_enb_disb=false; //Overide the enable or disable stepper driver settings
}conf;

enum differential_direction //Constants to set the direction pin
{
  LEFT_FORWARD=LEFT_ACLK,
  LEFT_BACKWARD=LEFT_CLK,
  RIGHT_FORWARD=RIGHT_CLK,
  RIGHT_BACKWARD=RIGHT_ACLK
};

//#############################################################DIFFERENTIAL PARAMETER############################################################
float wheel_radius;
float half_axle;
float max_diff_rpm=0;
float min_diff_rpm=0;
const float turn_angle=90.0;

//#############################################################UART STEPPER CONTROL##############################################################

//List of commands for the stepper motor
//Since the controller is not analog clear precise instuctions are used for the motor like move forward, backward etc...
enum cmd_list
{
  FRWD=109,         //Move forward
  BWRD=113,         //Move backward
  ROT_LEFT=127,     //Rotate robot left
  ROT_RIGHT=179,    //Rotate robot right  
  L_TURN_F=181,     //Turn left while moving forward
  R_TURN_F=191,     //Turn right while moving forward
  L_TURN_B=193,     //Turn left while moving backward
  R_TURN_B=197,     //Turn right while moving backward
  INVALID=255       //This an invalid command
};

typedef struct
{
  uint8_t ctrl_cmd=INVALID;
  uint8_t accl_enb=0;
  uint8_t brake_enb=0;
}ctrl_t; //Data of the type ctrl_t 

ctrl_t control;

//All the allowed motions are put into array for checking if the correct command is received
const uint8_t stepper_cmd_arr[8]={FRWD,BWRD,ROT_LEFT,ROT_RIGHT,L_TURN_F,R_TURN_F,L_TURN_B,R_TURN_B};

//#################################################################PAN TILT SERVOS################################################################

//Object of the modified servo library (Only works with MEGA2560)
ServoMod pan_servo,tilt_servo_l,tilt_servo_r;

//Servo pins
const uint8_t pan_servo_pin=9;
const uint8_t tilt_servo_pin_l=10;
const uint8_t tilt_servo_pin_r=11;

//To avoid the servo wrapping around 
const int MAX_PAN_ANGLE=170;
const int MIN_PAN_ANGLE=10;

const int MAX_TILT_ANGLE=170;
const int MIN_TILT_ANGLE=10;

//Servo pan and tilt positions
int pan_pos=90;
int tilt_pos=90;

void setup() {
  // put your setup code here, to run once:
  Serial.begin(115200);
  Serial1.begin(115200);  //Connects to /dev/serial0 of the RPi3B
  fonaSerial->begin(115200);

  pinMode(MCU_RDY_PIN,OUTPUT);
  digitalWrite(MCU_RDY_PIN,LOW); //This says microcontroller is not ready

  //For the stepper motors
  init_timer3_ctc(); //Initialising Timer 3
  init_timer4_ctc(); //Initialising Timer 4

  set_microstepping_pins(ms1,ms2);  //Microstepping set to 200 steps per revolution
  set_enable_pin(enb_l,enb_r,ENABLE_SMOT,false);  //Both the left and right motors are disabled and only of steps needs to be executed do they are enabled
  
  set_step_pins_LR(stp_l,stp_r);
  set_dir_pins_LR(dir_l,dir_r);
  
  set_rpm_left(MAX_RPM); //Set the RPM for left
  set_rpm_right(MAX_RPM); //Set the RPM for right

  differential_param(WHEEL_RADIUS,HALF_AXLE,MIN_RPM,MAX_RPM);

  //For the servo motors
  pan_servo.attach(pan_servo_pin);
  tilt_servo_l.attach(tilt_servo_pin_l);
  tilt_servo_r.attach(tilt_servo_pin_r);
  ctrl_pan_and_tilt(pan_pos,tilt_pos); //Move to correct postion during initialization

  //For initializing the sensors
  init_sensors_modules();

  digitalWrite(MCU_RDY_PIN,HIGH); //This says microcontroller is ready
}

void loop() {
  // put your main code here, to run repeatedly:
  receive_commands_and_execute(&control); //Get the command
  ctrl_cmd_execution(&control); //Change the stepper behaviour according to the command
  ctrl_pan_and_tilt(pan_pos,tilt_pos); //Pan and tilt the camera

  if(is_update_allowed(SENSOR_READING_DELAY))
  {
    read_check_send_gas_data();
    read_check_send_particle_data();
    read_send_environmental_data();
    send_alert_SMS();
  }
}

//#############################################################SENSORS AND PERIPHERALS############################################################

void init_sensors_modules()  // Function to initialize the sensors
{
  if(!fona.begin(*fonaSerial))  //Test the 3G module
  {
    Serial.println("\nSIM5320E 3G module not found!\n");
  }
  
  if(!particle_sensor.begin(Wire,I2C_SPEED_FAST)) //Use I2C at 400kHz and checking if the sensor is present
  {
    Serial.print("\nMAX30105 sensor not found!\n");
  }

  if(air_quality.begin() != 0)
  {
    Serial.print("CCS811 sensor not found!\n");
  }

  if(!bme.begin())
  {
    Serial.print("BME280 sensor not found!\n");
  }

  particle_sensor.setup(); //Configure the sensor
}

boolean is_update_allowed(unsigned long delay_millis) //Function to say whether the update should be done according to a set interval
{
  static unsigned long prev_millis;

  if((millis()-prev_millis)>delay_millis) 
  {
    prev_millis=millis();
    return true;
  }
  else return false;
}

void send_alert_SMS()  //Function to send an SMS alert
{
  if(alrt_com.sms_send && alrt_com.enable_sms && (alrt_com.sms_tries<alrt_com.max_tries) && !alrt_com.sms_repeat_disable) //If the sms is not sent
  { 
    if(is_registered_to_network()) //If the SIM is registered to the home network
    {
      if (!fona.sendSMS(alrt_com.sms_num,alrt_com.alert_msg)) //Sending the SMS alert
      {
        Serial.println("SMS alert failed to sent!");
        alrt_com.sms_send=true;
        alrt_com.sms_tries++;
      } 
      else 
      {
        Serial.println("SMS alert sent!");
        alrt_com.sms_tries=0; //Reset the tries
        alrt_com.sms_send=false;
        alrt_com.sms_repeat_disable=true; //The repeat is disabled 
      }
    }
    else
    {
      Serial.println("Not registered to any network, cannot send alert SMS");
    }
  }
}

boolean is_registered_to_network()  //Check if we are connected to the network
{
  if(fona.getNetworkStatus() == 1) return true;
  else return false;
}

void read_environmental_sensor(float &pres, float &temp, float &hum)  //Environmental sensor readings
{
  temp=bme.readTemperature(); //Degree Centigrade
  pres=bme.readPressure(); //Pascals (Pa)
  hum=bme.readHumidity();  // Percentage Relative Humidity (%RH)

  if(is_enviroment_update_allowed(300000))
  {
    air_quality.setEnvironmentalData(hum,temp); //Using the BME280 sensor to set the humidity and temperature for the air quality sensor
  } 
}

boolean is_enviroment_update_allowed(unsigned long delay_millis) //Function to say whether the update should be done according to a set interval
{
  static unsigned long prev_millis;
  static boolean init_update;  //Initial update

  if(!init_update)  // If the initial update of the environmental data is not
  {
    init_update=true;
    return true;
  }

  if((millis()-prev_millis)>delay_millis) 
  {
    prev_millis=millis();
    return true;
  }
  else return false;
}

void send_environmental_data(float pres, float temp, float hum) //Send the environmental sensor readings
{
  Serial1.print("e,");
  Serial1.print(pres);
  Serial1.print(',');
  Serial1.print(temp);
  Serial1.print(',');
  Serial1.print(hum);
  Serial1.println();
}

void read_send_environmental_data() //Send the environmental data
{
  float pressure,temperature,humidity;
  read_environmental_sensor(pressure,temperature,humidity);
  send_environmental_data(pressure,temperature,humidity);
}

void read_particle_sensor(unsigned int &r, unsigned int &g, unsigned int &ir)  //Particle sensor readings
{
  r=particle_sensor.getRed();
  g=particle_sensor.getGreen();
  ir=particle_sensor.getIR();
}

void send_particle_data(unsigned int r, unsigned int g, unsigned int ir)  //Send the particle sensor data
{
  Serial1.print("p,");
  Serial1.print(r);
  Serial1.print(',');
  Serial1.print(g);
  Serial1.print(',');
  Serial1.print(ir);
  Serial1.println();
}

void check_particle_data(unsigned int r, unsigned int g, unsigned int ir)  //Function to check for the required particle eg: smoke 
{
  if(r > thresh.red && g > thresh.green && ir > thresh.ir)
  {
    Serial.println("Particle threshold reached!");
    Serial.println("R= "+String(r)+" G= "+String(g)+" IR= "+String(ir));
    alrt_com.sms_send=true;

    String msg="Particle Alert\nRed= "+String(r)+"\nGreen= "+String(g)+"\nIR= "+String(ir);
    msg.toCharArray(alrt_com.alert_msg,(sizeof(alrt_com.alert_msg)/sizeof(char))); //The message to be sent is converted to a char array
  }
}

void read_check_send_particle_data() //Send particle data
{
  unsigned int red,green,ir;
  read_particle_sensor(red,green,ir);
  check_particle_data(red,green,ir);
  send_particle_data(red,green,ir);
}

void read_gas_sensor(unsigned int &eco2, unsigned int &tvoc)  //Gas sensor readings
{
  if(air_quality.dataAvailable()) // The data during the first 20 minutes are not accurate
  {
    air_quality.readAlgorithmResults();
    eco2=air_quality.getCO2();
    tvoc=air_quality.getTVOC();
  }
}

boolean is_gas_sens_wait_done(unsigned long delay_millis)  //Function to wait for the gas sensor readings to stabalize
{
  static boolean wait_done=false;
  static unsigned long prev_millis;

  if(((millis()-prev_millis)>delay_millis) && !wait_done)
  {
    wait_done=true;
    prev_millis=millis();
  }
  return wait_done;
}

void send_gas_readings(unsigned int eco2, unsigned tvoc)  //Send the gas sensor reading 
{
  if(is_gas_sens_wait_done(10000))
  {
    Serial1.print("g,");
    Serial1.print(eco2);
    Serial1.print(',');
    Serial1.print(tvoc);
    Serial1.println();
  }
}

void check_gas_data(unsigned int eco2, unsigned tvoc)
{
  if((eco2 > thresh.eCO2 || tvoc > thresh.TVOC) && is_gas_sens_wait_done(10000))
  {
    Serial.println("Gas Threshold reached");
    Serial.println("eCO2= "+String(eco2)+" TVOC= "+String(tvoc));
    alrt_com.sms_send=true;
    
    String msg="Air Quality Alert\neCO2= "+String(eco2)+" ppm\nTVOC= "+String(tvoc)+" ppb";
    msg.toCharArray(alrt_com.alert_msg,(sizeof(alrt_com.alert_msg)/sizeof(char))); //The message to be sent is converted to a char array
  }
}

void read_check_send_gas_data() //Send the gas readings
{
  unsigned int eCO2,TVOC;
  read_gas_sensor(eCO2,TVOC);
  check_gas_data(eCO2,TVOC);
  send_gas_readings(eCO2,TVOC);
}

//FUNCTION TO DEBUG THE SENSORS

void debug_bme280()
{
  float temp=bme.readTemperature(); //Degree Centigrade
  float pres=bme.readPressure(); //Pascals (Pa)
  float hum=bme.readHumidity();  // Percentage Relative Humidity (%RH

  Serial.print("Temperature= ");
  Serial.print(temp);
  Serial.print(" C");
  Serial.print(" Pressure= ");
  Serial.print(pres);
  Serial.print(" Pa");
  Serial.print(" Humidity= ");
  Serial.print(hum);
  Serial.print(" %RH");
  Serial.println();
}

void debug_max30105()
{
  Serial.print("R= ");
  Serial.print(particle_sensor.getRed());
  Serial.print(" IR= ");
  Serial.print(particle_sensor.getIR());
  Serial.print(" G= ");
  Serial.print(particle_sensor.getGreen());
  Serial.println();
}

void debug_ccs811()
{
  if(air_quality.dataAvailable()) // The data during the first 20 minutes are not accurate
  {
    air_quality.readAlgorithmResults();
    Serial.print("eCO2= ");
    Serial.print(air_quality.getCO2());
    Serial.print(" ppm");
    Serial.print(" TVOC= ");
    Serial.print(air_quality.getTVOC());
    Serial.print(" ppb");
    Serial.println();
  }
}

//#############################################################STEPPER DRIVER############################################################

ISR(TIMER3_COMPA_vect) //ISR for Timer 3
{
  OCR3A=left.req_count; //Updating the new count here as the counter TCNT3 is reset to 0 for this ISR to be called 
  
  if(((left.step_count < left.req_steps) || left.until_right_stops) && left.start_rotation)
  {
    if(conf.auto_enb_disb) digitalWrite(conf.enb_left,ENABLE_SMOT);
    digitalWrite(left.dir_pin,left.direct); //Set the direction of the motor to turn
    digitalWrite(left.step_pin,digitalRead(left.step_pin)^1); //Toggle the pin
    if(digitalRead(left.step_pin)) left.step_count++; //when ever the pin goes from LOW -> HIGH we get a step and therefore increment the counter
    if(left.req_steps-left.step_count <= BUF_STEPS) left.steps_completed=true; //This is allow for some buffer
    else left.steps_completed=false; //Steps are not completed
  }
  else 
  { 
    if(!conf.override_enb_disb && conf.auto_enb_disb) digitalWrite(conf.enb_left,DISABLE_SMOT);
    digitalWrite(left.step_pin,LOW); //If the last operation left the pin HIGH, set it LOW
    right.until_left_stops=false; //Because left has stopped rotating
    left.steps_completed=true;  //Steps are completed
    left.step_count=0;
    left.req_steps=0;
  }
}

ISR(TIMER4_COMPA_vect)
{
  OCR4A=right.req_count; 

  if(((right.step_count < right.req_steps) || right.until_left_stops) && right.start_rotation)
  {
    if(conf.auto_enb_disb) digitalWrite(conf.enb_right,ENABLE_SMOT);
    digitalWrite(right.dir_pin,right.direct);
    digitalWrite(right.step_pin,digitalRead(right.step_pin)^1);
    if(digitalRead(right.step_pin)) right.step_count++;
    if(right.req_steps-right.step_count <= BUF_STEPS) right.steps_completed=true;
    else right.steps_completed=false;
  }
  else
  {
    if(!conf.override_enb_disb && conf.auto_enb_disb) digitalWrite(conf.enb_right,DISABLE_SMOT);
    digitalWrite(right.step_pin,LOW);
    left.until_right_stops=false; //Because the right has stopped rotating
    right.steps_completed=true;
    right.step_count=0;
    right.req_steps=0;
  }
}

void set_step_pins_LR(uint8_t l_step_pin, uint8_t r_step_pin) //Set the pins for the step left and right
{
  left.step_pin=l_step_pin;
  right.step_pin=r_step_pin;

  pinMode(left.step_pin,OUTPUT);
  digitalWrite(left.step_pin,LOW); 

  pinMode(right.step_pin,OUTPUT);
  digitalWrite(right.step_pin,LOW);
}

void set_dir_pins_LR(uint8_t l_dir_pin, uint8_t r_dir_pin) //Set the direction pins
{
  left.dir_pin=l_dir_pin;
  right.dir_pin=r_dir_pin;

  pinMode(left.dir_pin,OUTPUT);
  digitalWrite(left.dir_pin,LOW);

  pinMode(right.dir_pin,OUTPUT);
  digitalWrite(right.dir_pin,LOW);
}

void set_microstepping_pins(uint8_t ms1, uint8_t ms2) // Set the MS pins
{
  conf.ms1=ms1;
  conf.ms2=ms2;

  pinMode(conf.ms1,OUTPUT);
  pinMode(conf.ms2,OUTPUT);

  /*
  DRV8834 microstepping setup table
  ------------------------------------------
  MS1        MS2    Microstepping Resolution
  ------------------------------------------
  Low        Low          Full step
  High       Low          Half step
  Floating   Low          1/4 step
  Low        High         1/8 step
  High       High         1/16 step
  Floating   High         1/32 step
  */

  //Currently set to Full Step Mode for the DRV8834
  digitalWrite(conf.ms1,LOW);
  digitalWrite(conf.ms2,LOW);
}

void set_enable_pin(uint8_t l_enb_pin, uint8_t r_enb_pin, boolean enb_or_disb, boolean auto_smot_enb) //Set the enable pin
{
  conf.enb_left=l_enb_pin;
  conf.enb_right=r_enb_pin;
  conf.auto_enb_disb=auto_smot_enb;

  pinMode(conf.enb_left,OUTPUT);
  pinMode(conf.enb_right,OUTPUT);
  
  digitalWrite(conf.enb_left,enb_or_disb); //HIGH to disable and LOW to enable
  digitalWrite(conf.enb_right,enb_or_disb); //HIGH to disable and LOW to enable
}

void set_rpm_left(float rpm) //Function to set the RPM (The count is updated to OCR3A register)
{
  //This function should not be called outside the setup function because of the counter might miss the compare when new value is written
  cli();
  left.req_count=calc_counts_to_compare(F_CLK_IO,PS1024,step_frequency(rpm,MS,DPS)); 
  OCR3A=left.req_count; //Set the required to the Output Compare Register for Timer 3 
  sei();
}

void set_rpm_right(float rpm) //Function to set the RPM (The count is updated to OCR4A register)
{
  //This function should not be called outside the setup function because of the counter might miss the compare when new value is written
  cli();
  right.req_count=calc_counts_to_compare(F_CLK_IO,PS1024,step_frequency(rpm,MS,DPS));
  OCR4A=right.req_count;
  sei();
}

void update_rpm_left(float rpm) //Function to update the RPM (The count is updated when the ISR is called)
{
  //This function can be called anywhere
  left.req_count=calc_counts_to_compare(F_CLK_IO,PS1024,step_frequency(rpm,MS,DPS));
}

void update_rpm_right(float rpm) //Function to update the RPM (The count is update when the ISR is called)
{
  //This function can be called anywhere
  right.req_count=calc_counts_to_compare(F_CLK_IO,PS1024,step_frequency(rpm,MS,DPS));
}

void rotate_motor_left(int steps, boolean direct, float rpm) //Function to add steps to be rotate the stepper
{
  left.req_steps=left.req_steps+steps;
  left.direct=direct;
  left.req_count=calc_counts_to_compare(F_CLK_IO,PS1024,step_frequency(rpm,MS,DPS)); //RPM is updated not set
}

void rotate_motor_right(int steps, boolean direct, float rpm)  //Function to add steps to be rotate the stepper
{
  right.req_steps=right.req_steps+steps;
  right.direct=direct;
  right.req_count=calc_counts_to_compare(F_CLK_IO,PS1024,step_frequency(rpm,MS,DPS));  //RPM is updated not set
}

boolean is_left_steps_completed()
{
  return left.steps_completed;
}

boolean is_right_steps_completed()
{
  return right.steps_completed;
}
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

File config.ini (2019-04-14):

[Connection]
host = 192.168.1.8
data_port = 8090
video_port = 8089

[Video_feed]
resolution = 7
fps = 20
color = 1
feed_type = 0
camera_wgt = 50.0
thermal_wgt = 50.0
enable_thermal = 0
thermal_scale = 1
thermal_vertical_pos = 0
thermal_horizontal_pos = 0
enable_hud = 1

[Video_rec]
vid_file_name = Video.avi
vid_file_path = ~\Documents\FumeBot\Video
vid_rec_res = 1
vid_rec_fps = 20
use_cap_res = 0
use_cap_fps = 0

[Training_rec]
train_file_name = training_dataset.npy
train_file_path = ~\Documents\FumeBot\Training
train_frame_width = 80
train_frame_height = 60
save_per_every = 250

[Ctrl_key_cfg]
forward = 0
backward = 0
left = 0
right = 0
l_turn_f = 0
r_turn_f = 0
l_turn_b = 0
r_turn_b = 0
accel = 0
brake = 0
forward_ord = 0
backward_ord = 1
left_ord = 2
right_ord = 3
l_turn_f_ord = 4
r_turn_f_ord = 5
l_turn_b_ord = 6
r_turn_b_ord = 7
accel_ord = 8
brake_ord = 9
disable_send_command = 0

[Pan_tilt_cfg]
pan_left = 0
pan_right = 180
tilt_up = 180
tilt_down = 0
pan_scaler = 4.0
tilt_scaler = 4.0
pan_tilt_enable = 1

[Gas_thresh]
eco2 = 1200
tvoc = 100

[Particle_thresh]
red = 10010
green = 1500
ir = 10999

[SMS_alert]
alert_number = 0987654321
alert_enable = 0

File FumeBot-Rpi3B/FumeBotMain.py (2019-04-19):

#!/usr/bin/python

"""
FUMEBOT CLIENT FOR RPI3B

This is the client to the FumeBot GUI program and is written to be run
on the Raspberry Pi side. This is the main python program that needs to
be executed. The program will spawn several threads for reading/sending
socket data and also for transmitting serial data to the Arduino and also
reading serial data.

Written by  :  Ajith Thomas
Date        :  5-4-2018
"""

import os
import time
import subprocess
from ConfigParser import ConfigParser
import RPi.GPIO as GPIO

from FumeBotModules.FumeBotSerialComm import FumeBotSerial
from FumeBotModules.FumeBotSocketComm import FumeBotSocket

# Status LED
RUNNING_LED=17
CONNECTED_LED=18
THREAD_RESTART_LED=27
RESET_AVR=22  # Pin that resets the Arduino if needed
MCU_RDY=23

# Configuration file for fumebot
CONFIG_FILE='bot_config.ini'
CONFIG_PATH='/home/pi/FumeBot-Rpi3B/'
config_path=os.path.join(CONFIG_PATH,CONFIG_FILE)

# Host address and Ports for socket communication
host = '192.168.1.8'
data_port = 8090
capture_port = 8089

# Serial port address
serial_port = '/dev/serial0'
baud = 115200

# Video capture settings
width=640
height=480
fps=15
color=0  # 0 for color and 1 for grayscale
res_index=0  # Which index was used in the GUI to set the above resolution
enable_thermal=0  # Thermal camera enabler or disable

# Gas sensor thresholds
eCO2_thresh=500
TVOC_thresh=15

# Particle sensor thresholds
red=1000
green=1500
ir=2000

# SMS alert settings
sms_number="00000000000"  # Number to send the sms alert
sms_enabled=0 # Enable the SMS alert to be sent (0 disabled and 1 enabled)

# Wifi status and signal level
wifi_connected=True  # If the wifi is not connected this will be changed any way (This is the case only if nothing critical depends on this)
wifi_quality=0
wifi_signal=0
wifi_check_delay=2  # Check for a wifi connection interval (seconds)
prev_check_time=0
wifi_status_set=False

serial_rx_header_dict={  # Headers used when the microcontroller sents data to RPi
	'GAS':'g',
	'ENVIRONMENT':'e',
	'PARTICLE':'p',
	'CFG_REQ':'cr',  # This is used to update all the configuration of the microcontroller
	'SER_SET_ACK':'ak',  #Serial acknowledgement for setting the configuration
}

config_sent_to_uC=False;

ack_code_dict={  # Acnowledgement codes
	'GAS_THR':1,  # Used in both serial and socket communication (This code is sent only when uC returns an acknowledge message)
	'PAR_THR':2,  # Used in both serial and socket communication (This code is sent only when uC returns an acknowledge message)
	'SMS_SET':3,  # Used in both serial and socket communication (This code is sent only when uC returns an acknowledge message)
	'CON_SET':4,  # Only for socket
	'VID_SET':5,  # Only for socket
	'RST_ALM':6,  # Used in both serial and socket communication (This code is sent only when uC returns an acknowledge message)
}

serial_tx_header_dict={  # Used to transmit data to the microcontroller
	'MOVE':'m',
	'CAM_PT':'c',
	'GAS_THR':'gt',
	'PAR_THR':'pt',
	'SMS':'sm',
	'RST_ALM':'ra',  # This should also reset other variables like SMS sent when threshold reached boolean and other associated variables
}

socket_send_header_dict={  # This is send header used only for sockets
	'GAS':'G',
	'ENVIRONMENTAL':'E',
	'PARTICLE':'P',
	'WIFI':'W',
	'SOCK_SET_ACK':'AK',  # To say that the socket command to set was successful
	'GAS_THR_RET': 'GTR',
    'PAR_THR_RET': 'PTR',
    'SMS_RET': 'SR',
    'CAM_RET': 'CMR',
    'MCU_STAT': 'MS',
}

socket_receive_header_dict={  # This is the receive header used only for sockets
	'MOVE':'MV',
	'CAM_PT':'CPT',
	'CAM_SET':'CM',
	'COM_SET':'CO',
	'GAS_THR':'GT',
	'PAR_THR':'PT',
	'SMS':'SM',
	'REBOOT_RPI':'RRP',
	'RESET_UC':'RUC',
	'PWR_OFF_RPI':'PWR',
	'RESET_ALARM': 'RA',  # Reset the alarm state in the microcontroller
    'RETRIEVE': 'RET',  # This is used to retrieve settings (The headers will be the parameter)
}

# Microcontroller status
mcu_ready_now=False

def handle_serial_receive(rx_data):  # Function to handle the incoming serial data from microcontroller
	
	try:
		parsed_data=rx_data.split(",")

		header=parsed_data[0]  # First item is the header which determine the type of data

		if header == serial_rx_header_dict['GAS']:  # Gas sensor readings
			
			eCO2=int(parsed_data[1])
			TVOC=int(parsed_data[2])

			cmd=format_socket_comm((socket_send_header_dict['GAS']), [eCO2, TVOC])

			soc_comm.put_socket_data(cmd)

		elif header == serial_rx_header_dict['PARTICLE']: # Particle sensor readings
			
			red=int(parsed_data[1])
			green=int(parsed_data[2])
			ir=int(parsed_data[3])

			cmd=format_socket_comm(socket_send_header_dict['PARTICLE'], [red, green, ir])

			soc_comm.put_socket_data(cmd)

		elif header == serial_rx_header_dict['ENVIRONMENT']:  # Environmental sensor readings
			
			pressure=float(parsed_data[1])
			temperature=float(parsed_data[2])
			humidity=float(parsed_data[3])

			cmd=format_socket_comm(socket_send_header_dict['ENVIRONMENTAL'], [pressure, temperature, humidity])

			soc_comm.put_socket_data(cmd)

		elif header == serial_rx_header_dict['CFG_REQ']:  # This is for when the uC asks for the configuration data

			print("Microcontroller requested configuration data")

			send_configuration_data_to_uC()

			print("Microcontroller configuration data sent")

		elif header == serial_rx_header_dict['SER_SET_ACK']:  # If acknowledgement code is received

			# Get the code
			ack_code=int(parsed_data[1])

			# The acknowledgement for the socket commands to set parameters for the microcontroller are sent here if the uC responds with the correct code
			if ack_code == ack_code_dict['GAS_THR']:
				cmd=format_socket_comm(socket_send_header_dict['SOCK_SET_ACK'],[ack_code])
				soc_comm.put_socket_data(cmd)

				print("Gas sensor threshold set")

			elif ack_code == ack_code_dict['PAR_THR']:
				cmd=format_socket_comm(socket_send_header_dict['SOCK_SET_ACK'],[ack_code])
				soc_comm.put_socket_data(cmd)

				print("Particle sensor threshold set")

			elif ack_code == ack_code_dict['SMS_SET']:
				cmd=format_socket_comm(socket_send_header_dict['SOCK_SET_ACK'],[ack_code])
				soc_comm.put_socket_data(cmd)

				print("SMS settings applied")

			elif ack_code == ack_code_dict['RST_ALM']:
				cmd=format_socket_comm(socket_send_header_dict['SOCK_SET_ACK'],[ack_code])
				soc_comm.put_socket_data(cmd)

				print("Alarm reset in microcontroller")

	except:  # If any error occurs just ignore it
		print("Serial receive error!")
		pass
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

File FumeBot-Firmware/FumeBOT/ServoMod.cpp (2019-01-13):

/*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
 Modified for FumeBot
 Modified by: Ajith Thomas
 Date: 25-6-2018
 */

#if defined(ARDUINO_ARCH_AVR)

#include <avr/interrupt.h>
#include <Arduino.h>

#include "ServoMod.h"

#define usToTicks(_us)    (( clockCyclesPerMicrosecond()* _us) / 8)     // converts microseconds to tick (assumes prescale of 8)  // 12 Aug 2009
#define ticksToUs(_ticks) (( (unsigned)_ticks * 8)/ clockCyclesPerMicrosecond() ) // converts from ticks back to microseconds


#define TRIM_DURATION       2                               // compensation ticks to trim adjust for digitalWrite delays // 12 August 2009

//#define NBR_TIMERS        (MAX_SERVOS / SERVOS_PER_TIMER)

static servo_t servos[MAX_SERVOS];                          // static array of servo structures
static volatile int8_t Channel[_Nbr_16timers ];             // counter for the servo being pulsed for each timer (or -1 if refresh interval)

uint8_t ServoCount = 0;                                     // the total number of attached servos


// convenience macros
#define SERVO_INDEX_TO_TIMER(_servo_nbr) ((timer16_Sequence_t)(_servo_nbr / SERVOS_PER_TIMER)) // returns the timer controlling this servo
#define SERVO_INDEX_TO_CHANNEL(_servo_nbr) (_servo_nbr % SERVOS_PER_TIMER)       // returns the index of the servo on this timer
#define SERVO_INDEX(_timer,_channel)  ((_timer*SERVOS_PER_TIMER) + _channel)     // macro to access servo index by timer and channel
#define SERVO(_timer,_channel)  (servos[SERVO_INDEX(_timer,_channel)])            // macro to access servo class by timer and channel

#define SERVO_MIN() (MIN_PULSE_WIDTH - this->min * 4)  // minimum value in uS for this servo
#define SERVO_MAX() (MAX_PULSE_WIDTH - this->max * 4)  // maximum value in uS for this servo

/************ static functions common to all instances ***********************/
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

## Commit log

2019-01-14 Added DNN initialize and activate buttons
2019-01-14 Interfaced new GUI buttons to appropriate functions
2019-01-16 Wifi checking failure corrected
    [FumeBotMain.py]
2019-01-19 Thread restart error fixed
    [FumeBotMain.py]

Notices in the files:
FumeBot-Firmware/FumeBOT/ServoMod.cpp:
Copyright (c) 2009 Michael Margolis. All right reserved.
